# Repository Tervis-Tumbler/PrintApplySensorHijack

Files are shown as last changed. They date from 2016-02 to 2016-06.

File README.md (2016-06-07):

# PrintApplySensorInterceptor
Intercepts the signal from the PrintApply box sensor and delays it according to applicator velocity.

## Parts list:
1 x 100uF, 50v electrolytic capacitor  
1 x 10uF, 50v electrolytic capacitor  
1 x Yellow LED  
1 x Red LED  
1 x P2N2222A transistor  
1 x 1K Ohm, 1W resistor  
2 x 10K Ohm, 1/6 resistor  
8 x 330 Ohm, 1/6 resistor  
1 x SPST lever microswitch  
1 x Breakaway pin headers, 24 pin minimum  
2 x Sparkfun RJ45 breakout boards  
2 x Sparkfun RJ45 connectors (non-MagJack)  
1 x Arduino Enclosure  
1 x mini breadboard and wiring kit  
http://www.amazon.com/Boundto-120PCS-Breadboard-Solderless-Prototype/dp/B017FXDLE6  
1 x Addicore L7805CV 5v voltage regulator  
1 x TO-220 Heatsink, 2.5W  
1 x #6-1/4 hex cap screw  
1 x #6 washer  
1 x #6 nut  

## Example output from the Arduino
Starting...  

Minimum Velocity: 1000  
Maximum Velocity: 55000  
Minimum Delay Time: 10  
Maximum Delay Time: 100  
  
Ready!  
Collecting accelerometer data...  
Box detected!  
Random Stroke Delay: 76 ms  
Velocity: 15985  
  
Waiting...  
Collecting accelerometer data...  
Box detected!  
Random Stroke Delay: 25 ms  
Velocity: 46485  
  
Waiting...  
Collecting accelerometer data...  
Box detected!  
Random Stroke Delay: 18 ms  
Velocity: 50725  
  
Waiting...  

## Schematic

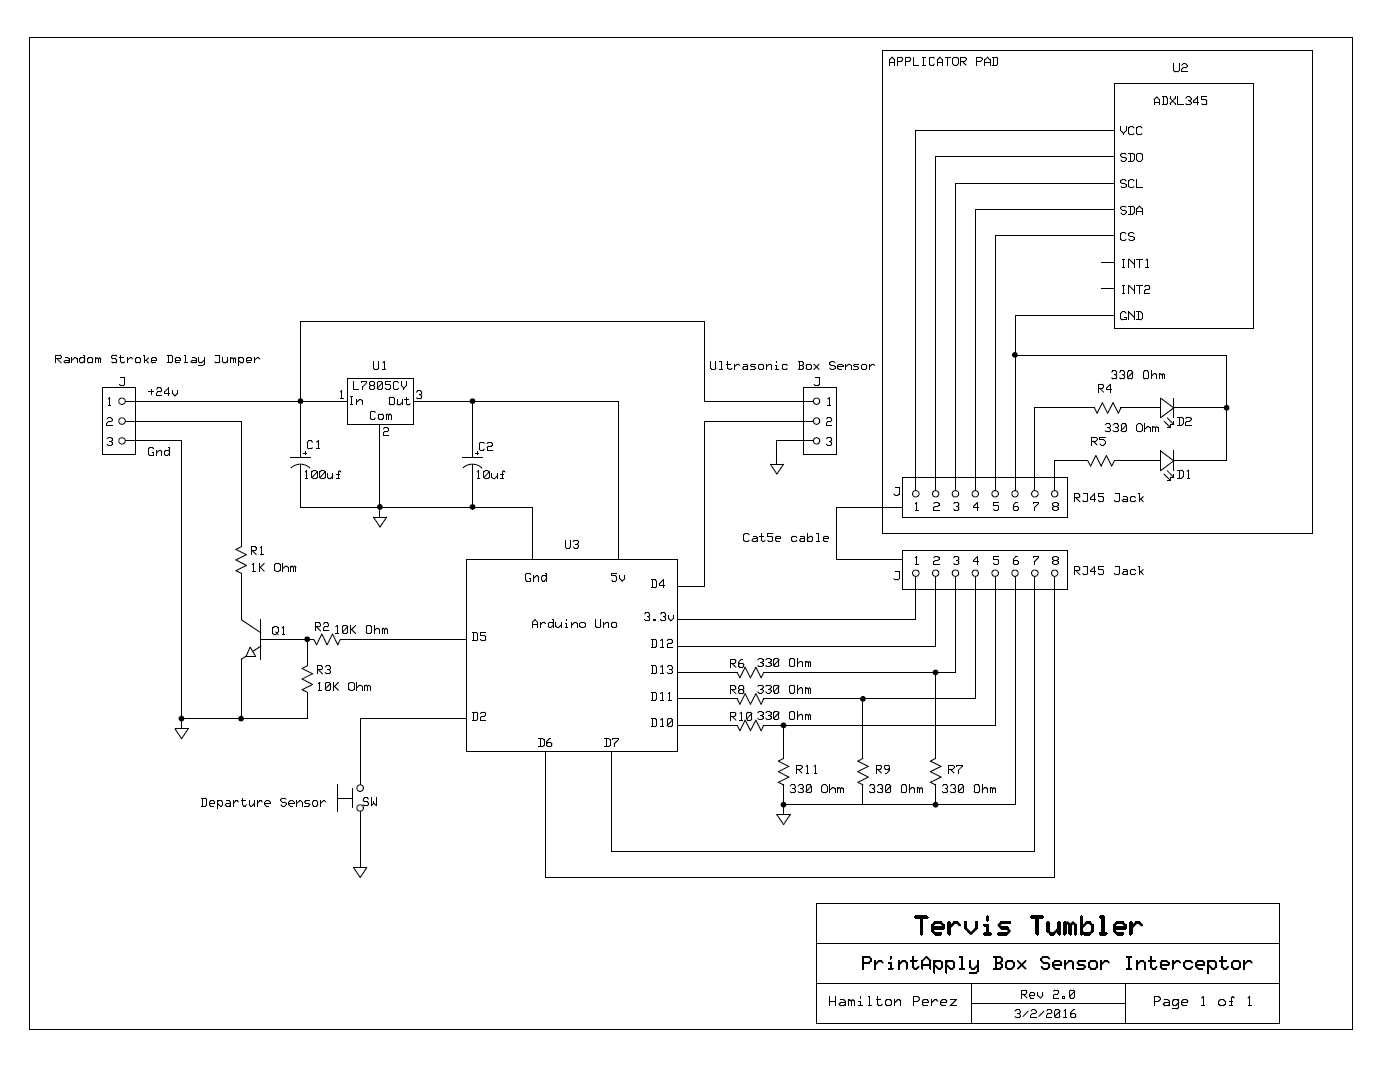
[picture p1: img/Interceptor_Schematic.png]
PrintApplySensorInterceptor Schematic
  
 
## Pictures in production
 
PrintApplySensorInterceptor inside FoxIV Mod6  

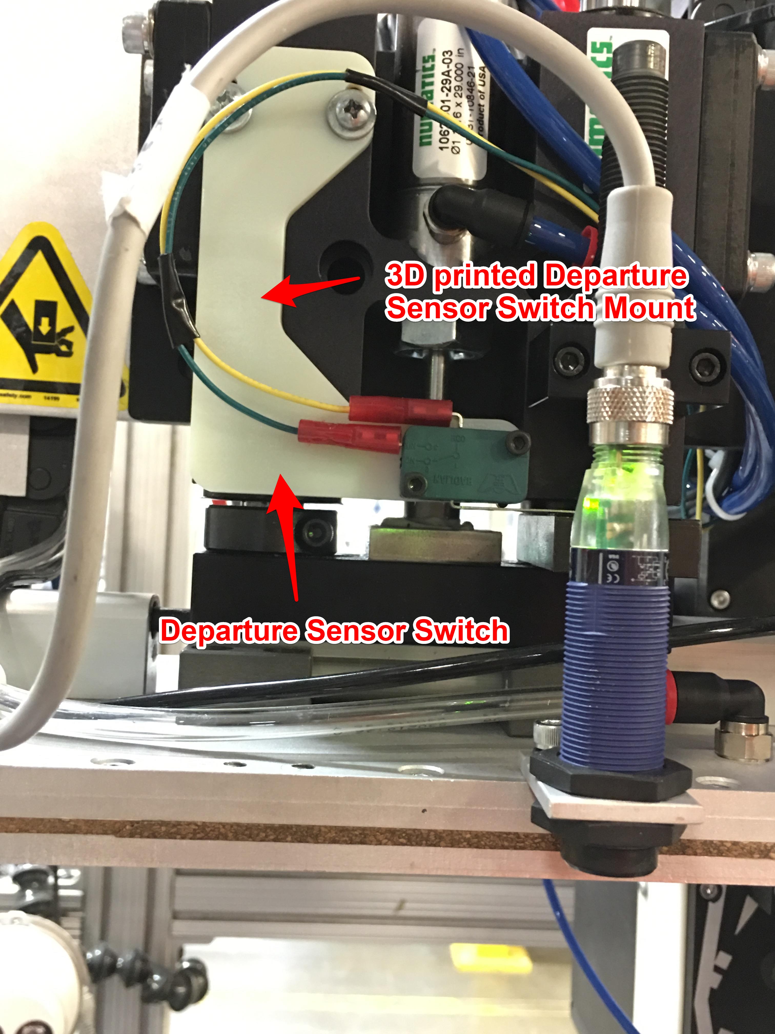
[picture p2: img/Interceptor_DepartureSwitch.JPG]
Departure Sensor Switch placement
  

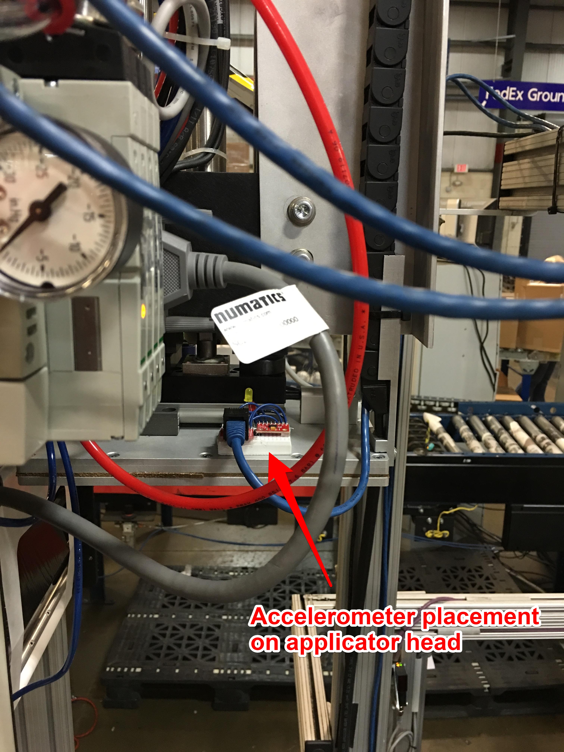
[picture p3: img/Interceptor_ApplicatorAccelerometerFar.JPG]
ADXL345 placement on applicator


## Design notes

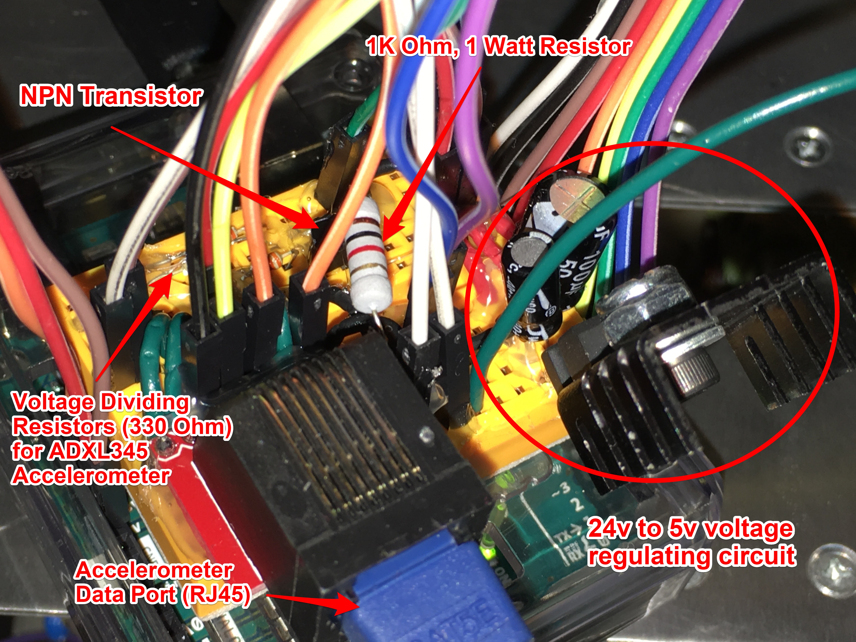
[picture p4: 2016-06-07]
img/Interceptor_CircuitBoard.JPG

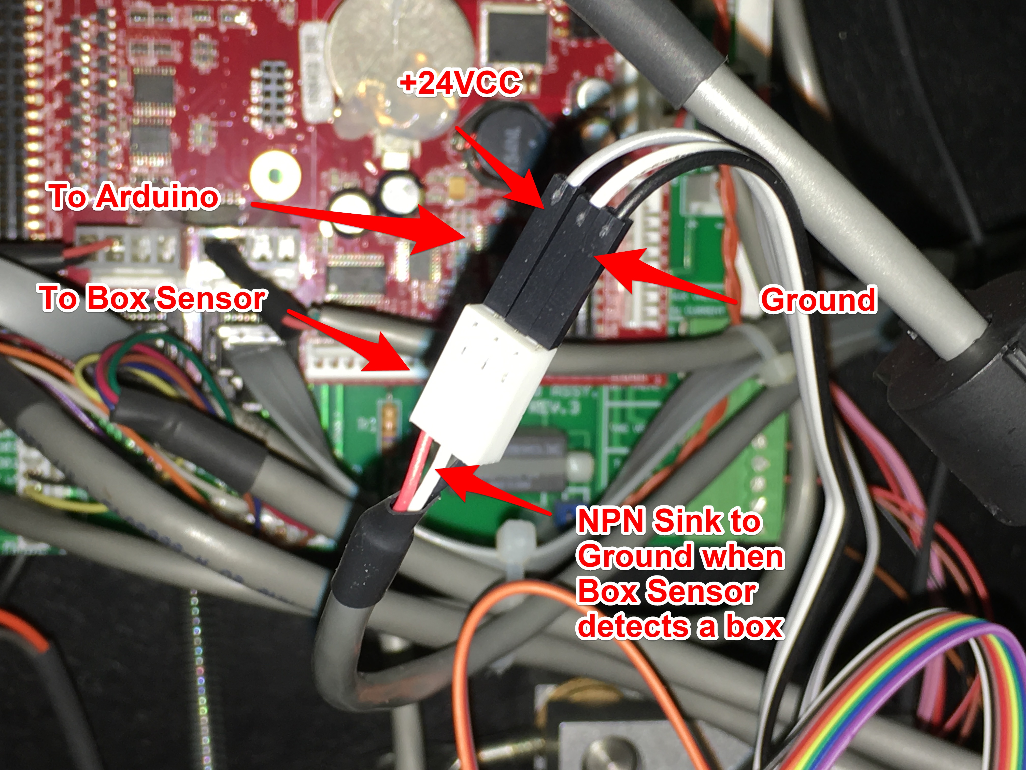
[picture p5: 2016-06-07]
img/Interceptor_BoxSensorJumper.JPG

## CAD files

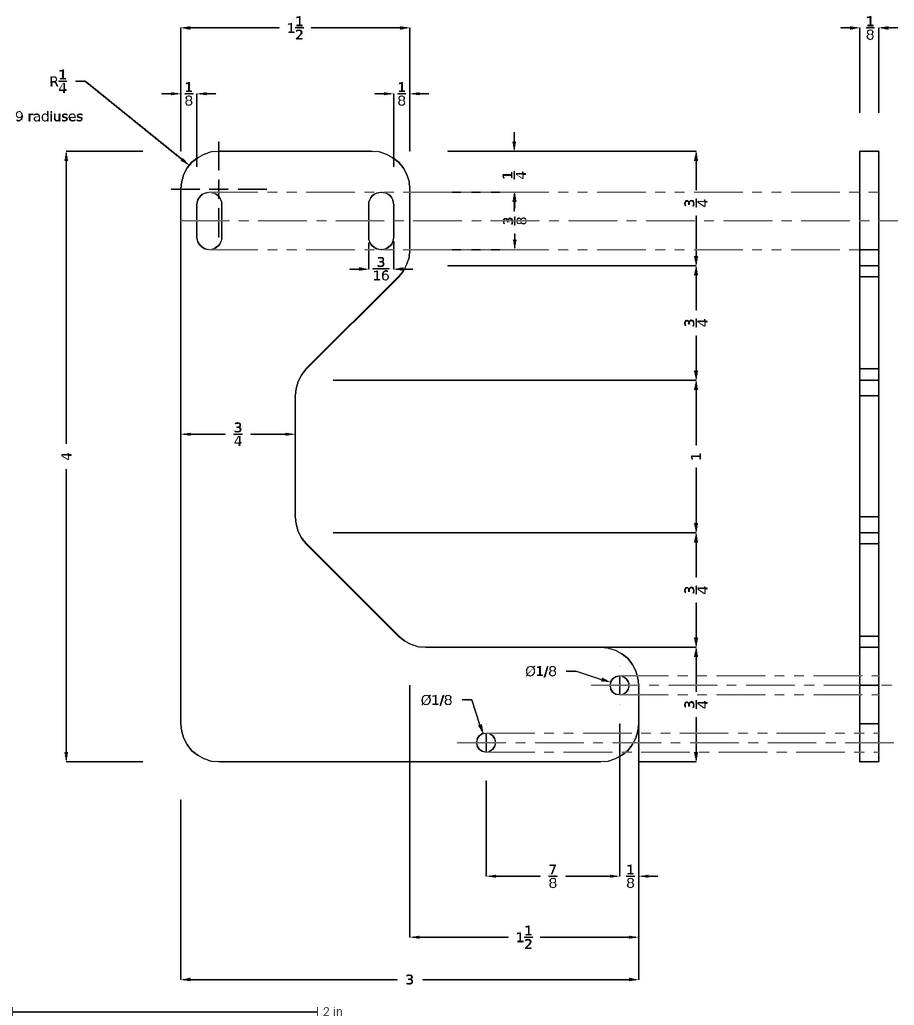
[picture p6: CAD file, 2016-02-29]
DepartureSensorSwitchMount.dxf
11/2
3/4
4
3
1/4
R1/4
9 radiuses
3/8
3/16
1
1/8
7/8
Ø1/8

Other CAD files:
DepartureSensorSwitchMount.dwg

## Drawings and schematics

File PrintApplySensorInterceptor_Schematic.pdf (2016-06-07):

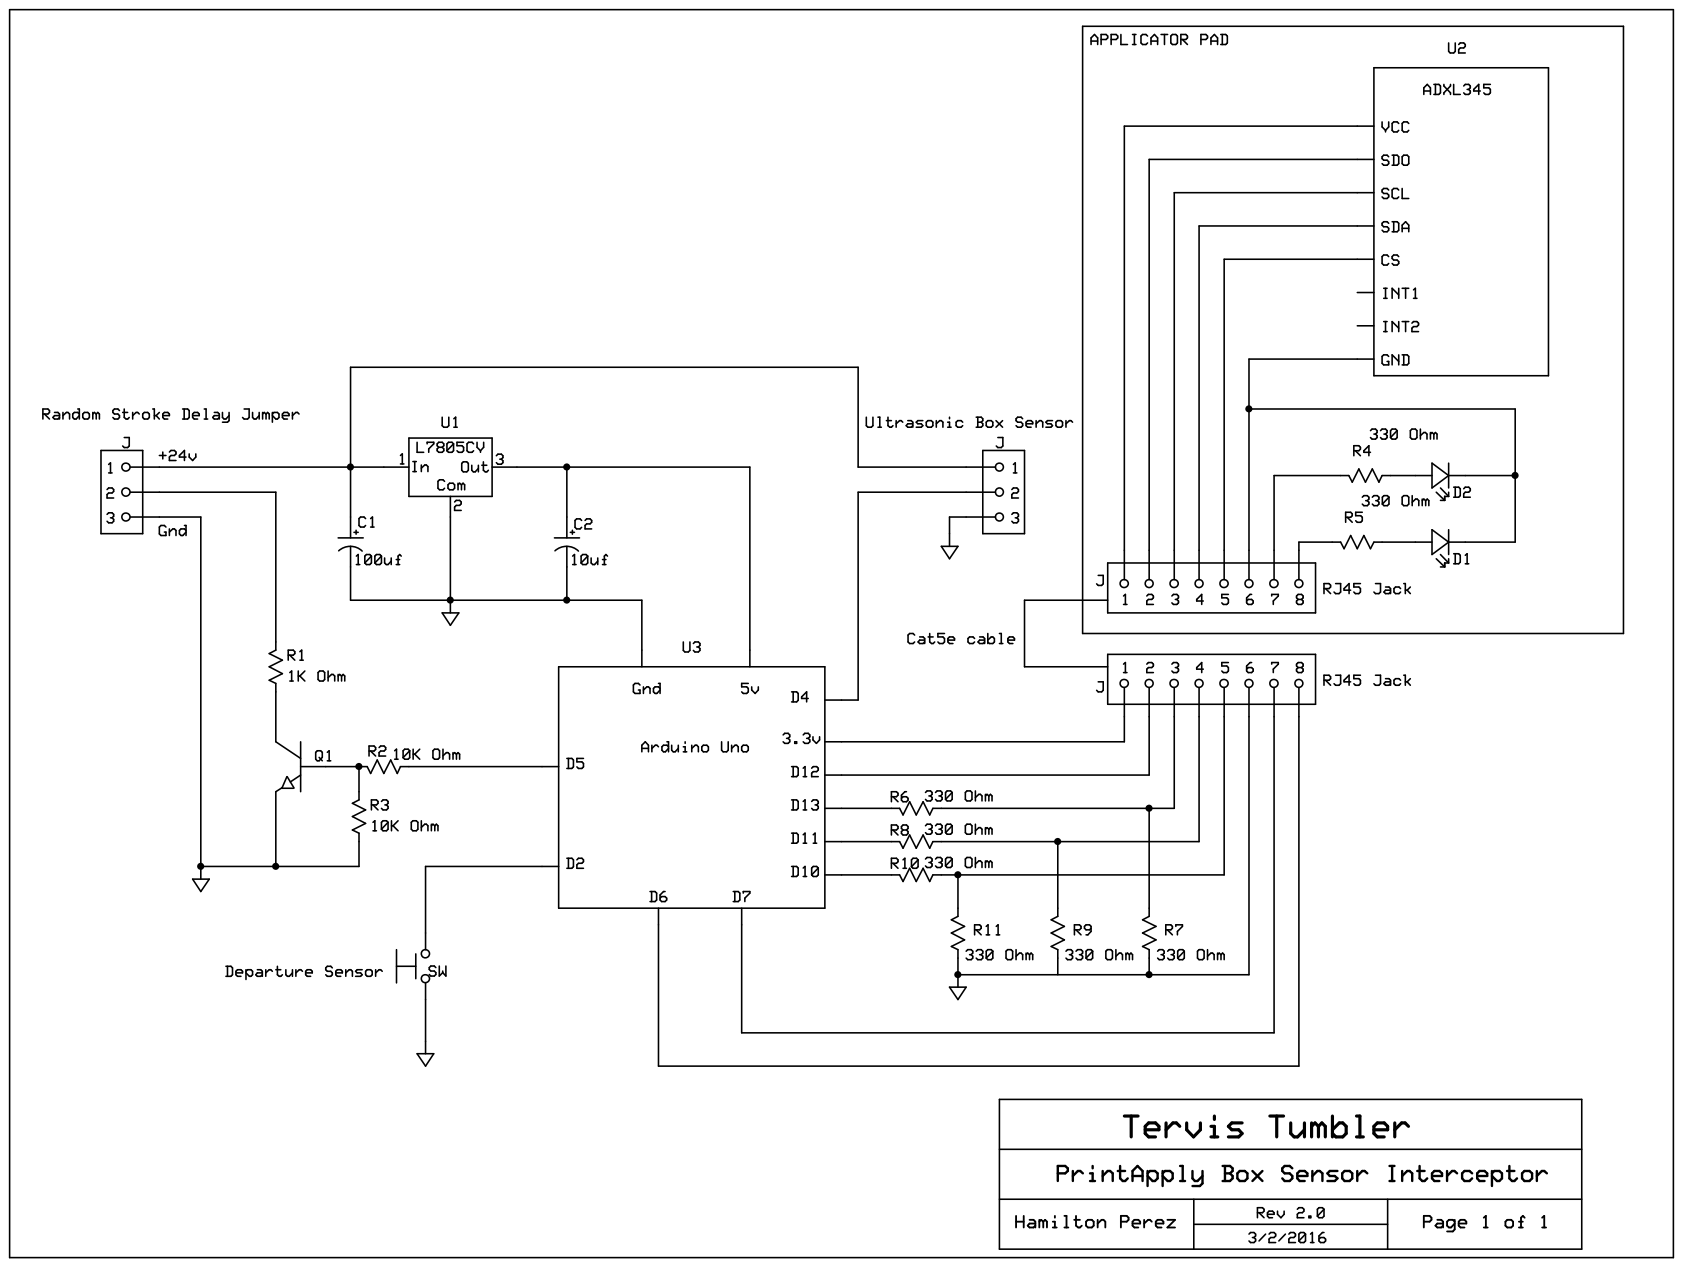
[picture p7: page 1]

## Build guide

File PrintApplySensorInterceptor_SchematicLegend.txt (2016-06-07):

Schematic map:
C1	100uf, 50v
C2	10uf, 50v
D1	LED - Yellow
D2	LED - Red
Q1	P2N2222A	
R1	1K Ohm	1K Ohm, 1W
R2	10K Ohm	10K Ohm, 1/6W
R3	10K Ohm	10K Ohm, 1/6W
R4	330 Ohm	330 Ohm, 1/6W
R5	330 Ohm	330 Ohm, 1/6W
R6	330 Ohm	330 Ohm, 1/6W
R7	330 Ohm	330 Ohm, 1/6W
R8	330 Ohm	330 Ohm, 1/6W
R9	330 Ohm	330 Ohm, 1/6W
R10	330 Ohm	330 Ohm, 1/6W
R11	330 Ohm	330 Ohm, 1/6W
SW	Microswitch, Lever, SPST
U1	L7805CV	Addicore L7805CV +5v
U2	Sparkfun ADXL345 Breakout Board
U3	Arduino Uno R3

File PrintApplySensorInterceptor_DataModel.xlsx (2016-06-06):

Delay in ms | Velocity | New Delay
106 | 19435 | 93
104 | 37270 | 46
106 | 33525 | 56
104 | 35015 | 52
50 | 34810 | 53 | Changing these values will change the data plot below
52 | 36395 | 48
52 | 35665 | 50 | Experimental values |  | Original values
52 | 37940 | 44 | minVelocityToCalculate | 1000 | 1000
50 | 30925 | 63 | maxVelocityToCalculate | 37500 | 37500
50 | 38905 | 42 | minRandomStrokeDelayTime | 45 | 45
62 | 28745 | 68 | maxRandomStrokeDelayTime | 140 | 140
57 | 29815 | 66
62 | 29070 | 67
63 | 32775 | 58
66 | 36500 | 48
59 | 36880 | 47
90 | 32275 | 59
90 | 39295 | 41
89 | 18300 | 95
50 | 34405 | 54
50 | 37860 | 45
57 | 31650 | 61
50 | 35310 | 51
55 | 33450 | 56
50 | 34370 | 54
50 | 34940 | 52
50 | 33290 | 56
62 | 11905 | 112
50 | 34230 | 54
52 | 30445 | 64
50 | 29235 | 67
55 | 28740 | 68
50 | 14170 | 106
120 | 35035 | 52
114 | 30235 | 64
119 | 19085 | 93
54 | 33190 | 57
50 | 32745 | 58
59 | 34220 | 54
50 | 34110 | 54
119 | 40525 | 38
54 | 34320 | 54
118 | 34950 | 52
118 | 36430 | 48
50 | 32680 | 58
50 | 36300 | 49
50 | 36820 | 47
65 | 33650 | 56
50 | 33615 | 56
70 | 33455 | 56
118 | 33675 | 55
63 | 13050 | 109
60 | 36295 | 49
50 | 34220 | 54
68 | 35880 | 50
50 | 35335 | 51
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

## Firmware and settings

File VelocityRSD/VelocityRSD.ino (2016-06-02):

#include <SPI.h>

// Intercepted signals.
int boxSensorPin = 4;
int randomStrokeDelayOutputPin = 5;

// LED status pins
int redLED = 7;
int yellowLED = 6;

// Accelerometer cable select
int spiCableSelect = 10;

long accelerometerCurveArea = 0;
int accelerometerSampleDelay = 5;
int applicatorHomePositionSensor = 2;
int cycleDelay = 2000;
int randomStrokeDelay;
int registerAddress;
long minVelocityToCalculate = 9000;
long maxVelocityToCalculate = 45000; //37500
int maxRandomStrokeDelayTime = 120; // +15 to compensate for overpacked large boxes
int minRandomStrokeDelayTime = 30; // +5 to compensate for overpacked small boxes

SPISettings settingsA(400000,MSBFIRST,SPI_MODE3);

void initiateAccelerometer (){

  SPI.begin();
  pinMode(spiCableSelect,OUTPUT);
  digitalWrite(spiCableSelect,HIGH);

  SPI.beginTransaction(settingsA);
  digitalWrite(spiCableSelect,LOW);

//  PowerCtl 
  registerAddress = 0x2D;
  registerAddress = registerAddress | 0x40;
  SPI.transfer(registerAddress);
  SPI.transfer(0x08);

  digitalWrite(spiCableSelect,HIGH);
  delay(1);
  digitalWrite(spiCableSelect,LOW);

//  Data Format
  registerAddress = 0x31;
  registerAddress = registerAddress | 0x40;
  SPI.transfer(registerAddress);
  SPI.transfer(0x0B);

  digitalWrite(spiCableSelect,HIGH);
  delay(1);
  digitalWrite(spiCableSelect,LOW);

//  DataRate
  registerAddress = 0x2C;
  registerAddress = registerAddress | 0x40;
  SPI.transfer(registerAddress);
  SPI.transfer(0x0D);
  
  digitalWrite(spiCableSelect,HIGH);
  delay(1);
}

int getZ(){
  digitalWrite(spiCableSelect,LOW);

//  Get Z data
  registerAddress = 0x36;
  registerAddress = registerAddress | 0x40; // Multiple bytes
  registerAddress = registerAddress | 0x80; // Read operation
  int a = SPI.transfer(registerAddress);
  int b = SPI.transfer(0x00);
  int c = SPI.transfer(0x00);
  digitalWrite(spiCableSelect,HIGH);

//  Combine bytes
  int result;
  result  = ((c << 8) | b) + 7;
  if ( result > 240 && result < 260 ) {
    return 250;
  }
  else {
  return result;    
  }
}

int calculateRandomStrokeDelay(long input) {
  if (input < minVelocityToCalculate){
    return maxRandomStrokeDelayTime;
  }
  else if (input > minVelocityToCalculate && input < maxVelocityToCalculate){
    return map(input,minVelocityToCalculate,maxVelocityToCalculate,maxRandomStrokeDelayTime,minRandomStrokeDelayTime);
  }
  else {
    return minRandomStrokeDelayTime;
  }
}

void printStatus(int randomStrokeDelay, long accelerometerCurveArea){
  Serial.print("Random Stroke Delay: ");
  Serial.print(randomStrokeDelay);
  Serial.println(" ms");
  Serial.print("Velocity: ");
  Serial.println(accelerometerCurveArea);
  Serial.println("");
}

bool isApplicatorMoving () {
  if (digitalRead(applicatorHomePositionSensor)){
    digitalWrite(yellowLED,HIGH);
    return true;
  }
  else {
    return false;
  }
}

bool boxDetected() {
  if (digitalRead(boxSensorPin)) {
    return false;
  }
  else {
    return true;
  }
}

void sendRandomStrokeDelaySignal () {
  digitalWrite(redLED,HIGH);
  delay(randomStrokeDelay);
  digitalWrite(randomStrokeDelayOutputPin,HIGH);
  delay(cycleDelay);
  digitalWrite(yellowLED,LOW);
  digitalWrite(redLED,LOW);
  digitalWrite(randomStrokeDelayOutputPin,LOW);   
}

void printSettings() {
  Serial.println("");
  Serial.print("Minimum Velocity: ");
  Serial.println(minVelocityToCalculate);
  Serial.print("Maximum Velocity: ");
  Serial.println(maxVelocityToCalculate);
  Serial.print("Minimum Delay Time: ");
  Serial.println(minRandomStrokeDelayTime);  
  Serial.print("Maximum Delay Time: ");
  Serial.println(maxRandomStrokeDelayTime);
  Serial.println("");
  
}

void setup() {
  Serial.begin(9600);
  Serial.println("Starting...");
  pinMode(applicatorHomePositionSensor,INPUT_PULLUP);
  pinMode(boxSensorPin,INPUT_PULLUP);
  pinMode(randomStrokeDelayOutputPin,OUTPUT);
  pinMode(redLED,OUTPUT);
  pinMode(yellowLED,OUTPUT);
  initiateAccelerometer();
  printSettings();
  Serial.println("Ready!");
}

void loop() {
  if (isApplicatorMoving()) {
    Serial.println("Collecting accelerometer data...");
    while (!boxDetected()){
      delay(accelerometerSampleDelay);  
      accelerometerCurveArea += (((getZ()*-1)+250) * accelerometerSampleDelay);
    }
    
    Serial.println("Box detected!");
    randomStrokeDelay = calculateRandomStrokeDelay(accelerometerCurveArea);
    printStatus(randomStrokeDelay,accelerometerCurveArea);
    sendRandomStrokeDelaySignal();
    accelerometerCurveArea = 0;
    Serial.println("Waiting...");
  }

  else{
    delay(1);
  }

}

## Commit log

2016-02-05 Create PrintApplySensorHijack.ino
    Main Arduino program.
2016-02-05 Update PrintApplySensorHijack.ino
    Created function to handle Random Stroke Delay time. Accepts delay in milliseconds and LED status light as parameters.
2016-02-05 Desktop commit
    Added schematics, current Arduino sketch.
    [PrintApplyBoxSensorInterceptor.sch]
2016-02-09 Fixed sensor polling, added medium box function.
    Reduced sensor polling from 25 ms to 1 ms to avoid interference with
    delay times. Added ability to detect medium boxes and delay signal
    accordingly.
2016-02-10 Tweaked values of delays, added console output.
    Console output now displays distance of ultrasonic sensor from
    applicator and the type of box detected.
    [PrintApplyBoxSensorInterceptor.sch]
2016-02-19 Created Velocity-based hijack
    This hijack is still in progress
    [PrintApplyBoxSensorInterceptor.sch]
2016-02-29 Created bracket CAD file, modified VelocityRSD
    VelocityRSD no longer depends on an interrupt from the applicator home
    position sensor. It is now polled every millisecond.
    [DepartureSwitchMount.dwg, DepartureSwitchMount.dxf]
2016-03-01 Updated values for velocity and Random Stroke Delay times.
2016-03-02 Created new schematic under VelocityRSD
    [PrintApplyBoxSensorHijack_Schematic.sch, VelocityRSD_Schematic.sch]
2016-03-25 Updated parts lists and values for VelocityRSD
    [VelocityRSD_model.xlsx]
2016-04-06 New updated default values
    [VelocityRSD_model.xlsx]
2016-06-06 Restructured repo contents
    - Updated variables on PrintApplySensorInterceptor sketch
    - Updated schematic to include Cat5e connection
    - Updated parts list to be clearer
    - Removed images of ultrasonic-based Arduino
    [PrintApplyBoxSensorHijack_Schematic.sch, PrintApplySensorInterceptor_DataModel.xlsx, PrintApplySensorInterceptor_Schematic.sch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]
2016-06-07 Added pictures of project
    - Added annotated images of projected mounted on the PrintApply
    - Renamed schematics
2016-06-07 Clarified Arduino sketch
    [DepartureSensorSwitchMount.dwg, DepartureSensorSwitchMount.dxf, PrintApplySensorInterceptor_Schematic.sch]
2016-06-07 Added Schematic image
2016-06-08 Output number of samples used to calculate velocity
